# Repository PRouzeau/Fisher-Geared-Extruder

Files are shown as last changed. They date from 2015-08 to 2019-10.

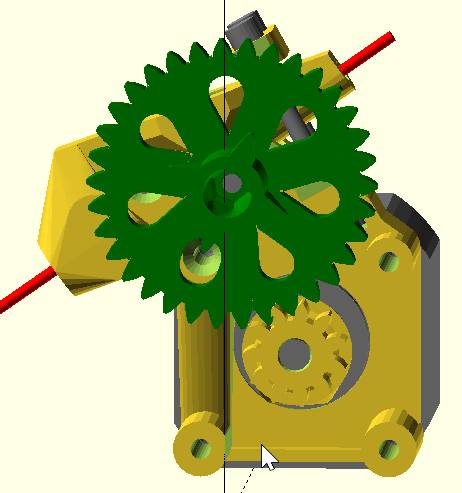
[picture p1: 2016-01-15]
Extruder_normal_pos.jpg

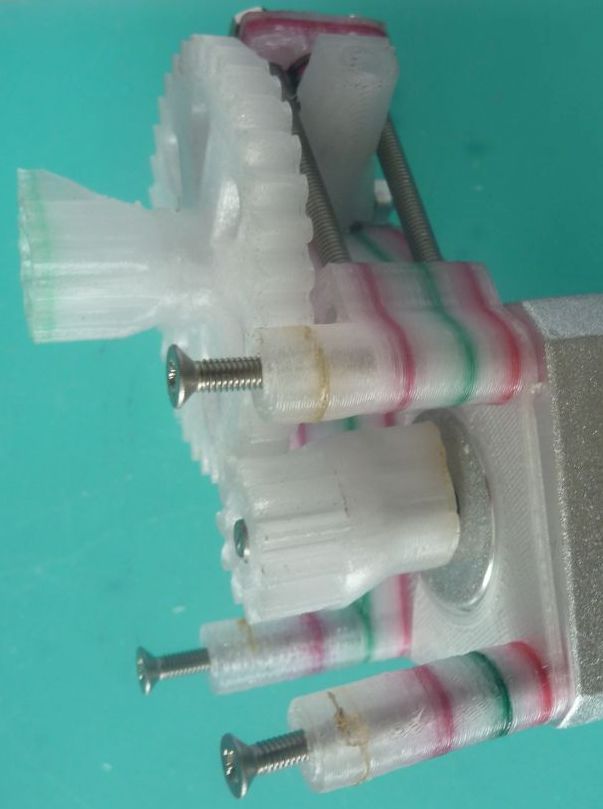
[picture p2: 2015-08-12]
Pres03.jpg

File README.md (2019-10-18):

# Geared-Extruder
Compact geared Extruder for bowden tube, side panel mount or top mount
designed initially for the Fisher Delta, used a mirrored version for the HXM.
Option with bearings 623 or MR93 (as supplied in Fisher 1)

To install OpenSCAD applications and models, see http://rouzeau.net/Print3D/OpenSCADApplications

Pour installer les applications et modèles OpenSCAD, voir  http://rouzeau.net/OpenSCAD/Applications

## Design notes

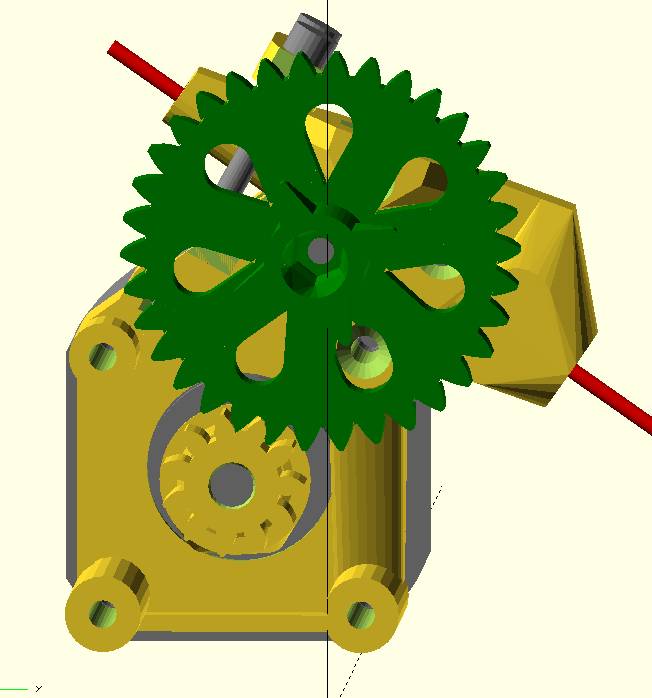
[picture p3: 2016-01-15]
Extruder_mirrored.jpg

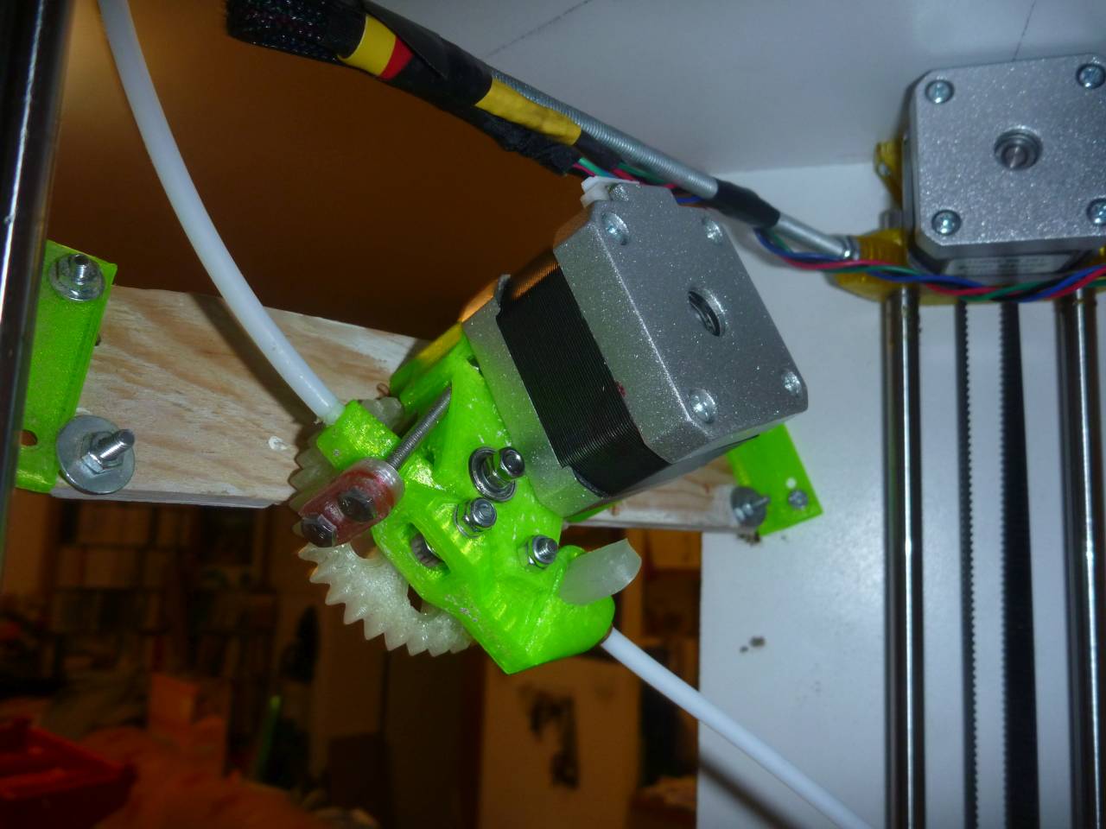
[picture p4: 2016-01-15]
HXM_extruder.JPG

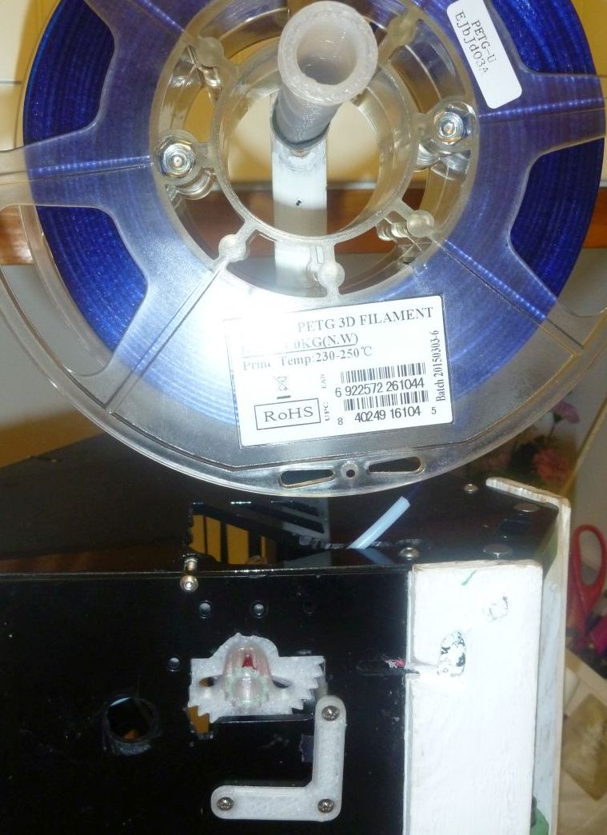
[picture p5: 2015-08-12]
Pres00.jpg

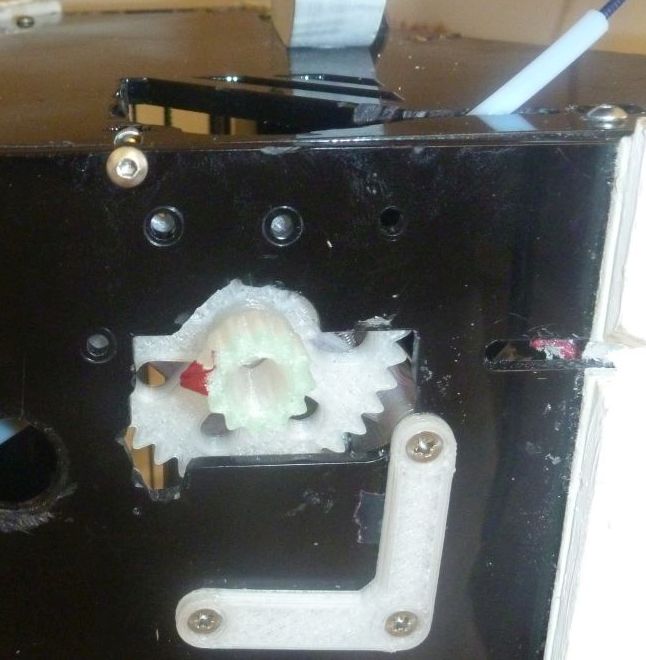
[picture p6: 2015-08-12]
Pres01.jpg

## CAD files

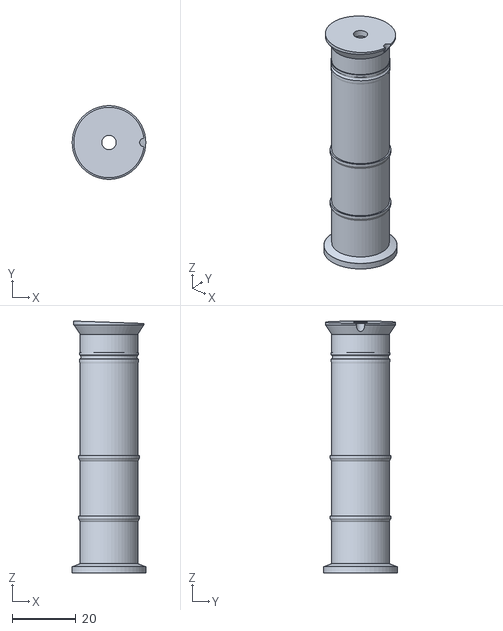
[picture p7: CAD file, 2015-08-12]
spigot80.stl
23.2 x 23.2 x 79.3

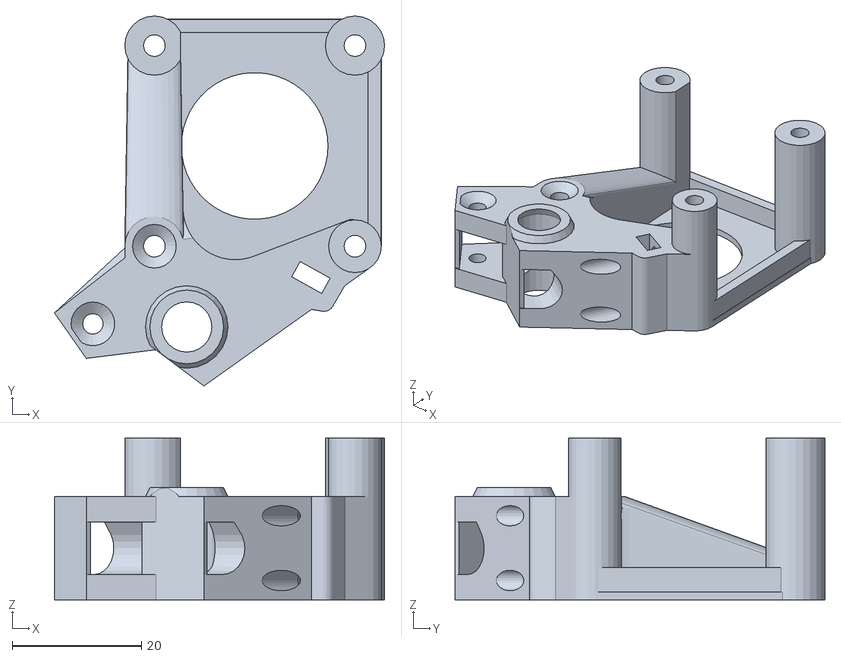
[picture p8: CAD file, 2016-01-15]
STL/Base_BB_MR93_mirrored.stl
51.0 x 57.2 x 25.0

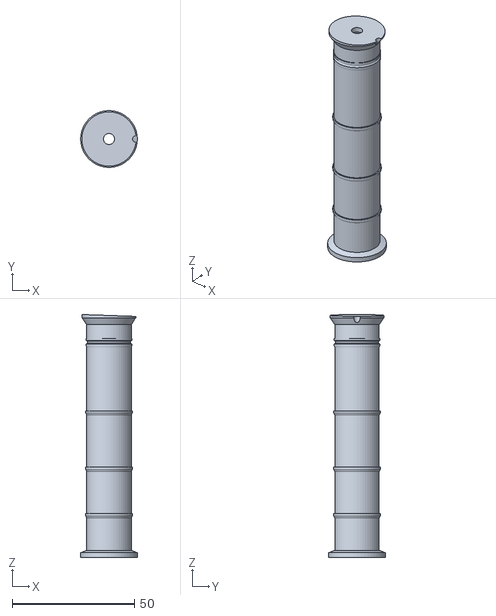
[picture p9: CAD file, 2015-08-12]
spigot100.stl
23.2 x 23.2 x 99.3

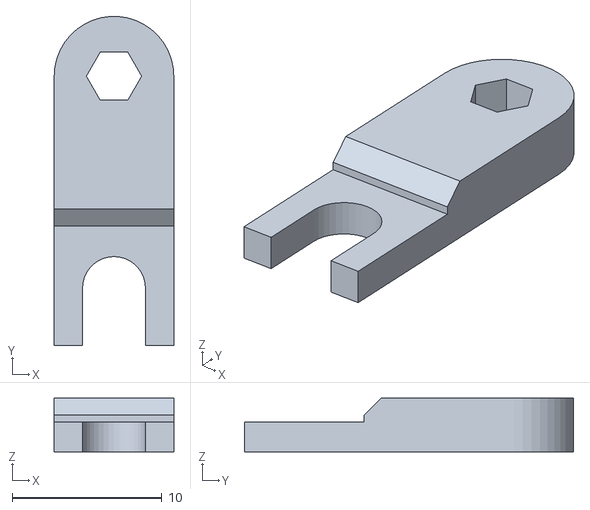
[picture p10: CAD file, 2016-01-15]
STL/tongue.stl
8.00 x 22.0 x 3.60

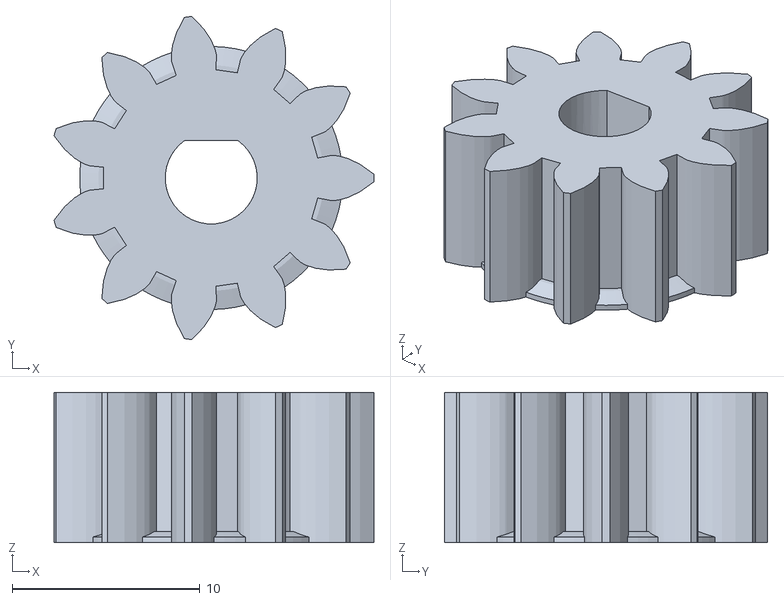
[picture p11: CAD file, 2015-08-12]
ormerod_small-gear.stl
17.0 x 17.2 x 8.00

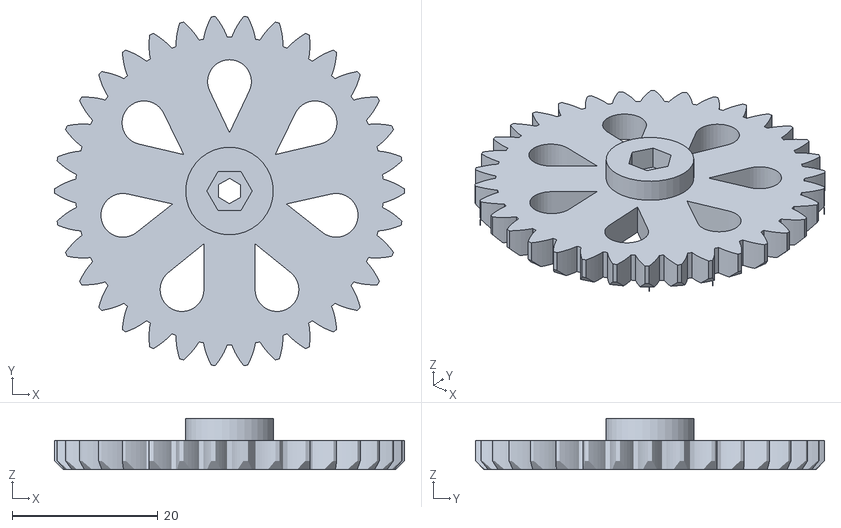
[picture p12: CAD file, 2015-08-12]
ormerod_large-gear.stl
48.0 x 47.8 x 7.00

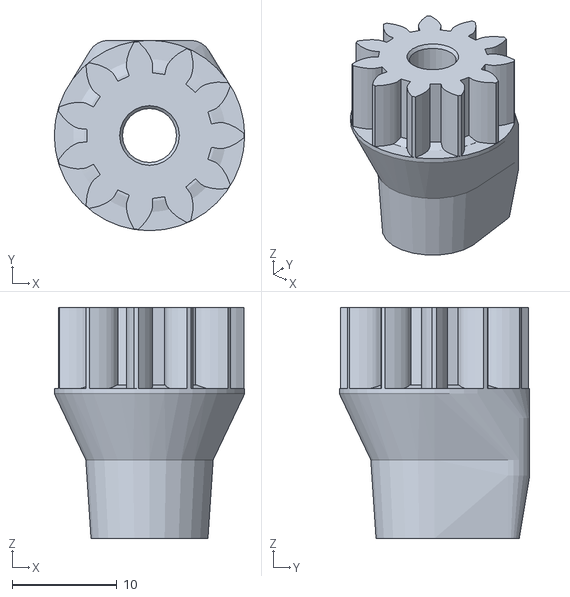
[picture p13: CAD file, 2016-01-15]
STL/PinionSize1.stl
18.1 x 18.1 x 22.0

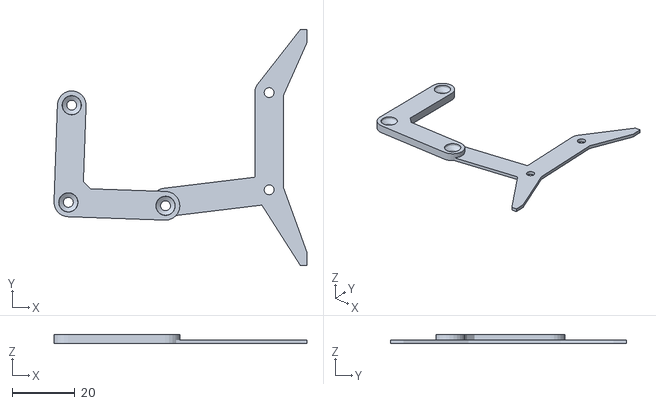
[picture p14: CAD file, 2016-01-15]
STL/motor_link_Fisher.stl
80.6 x 75.2 x 3.00

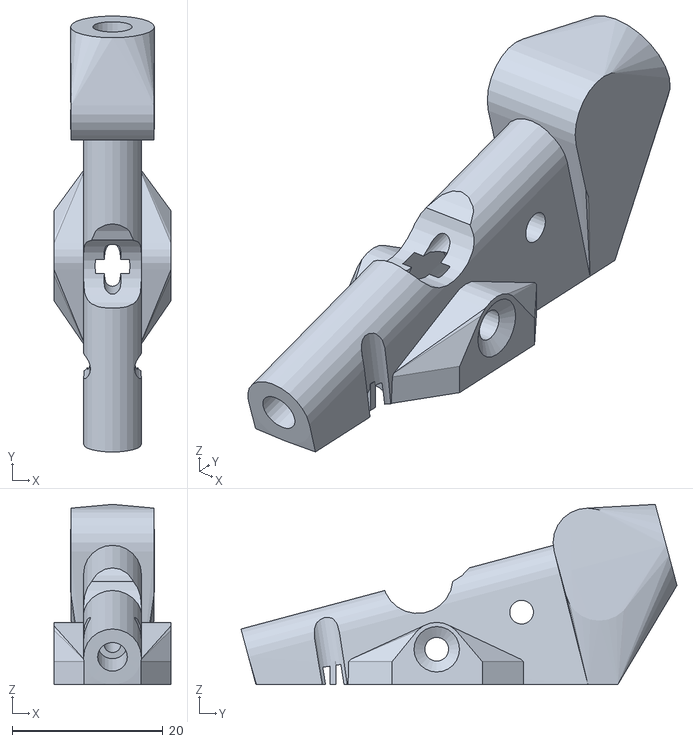
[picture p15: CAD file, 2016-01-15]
STL/lever.stl
15.5 x 57.9 x 23.9

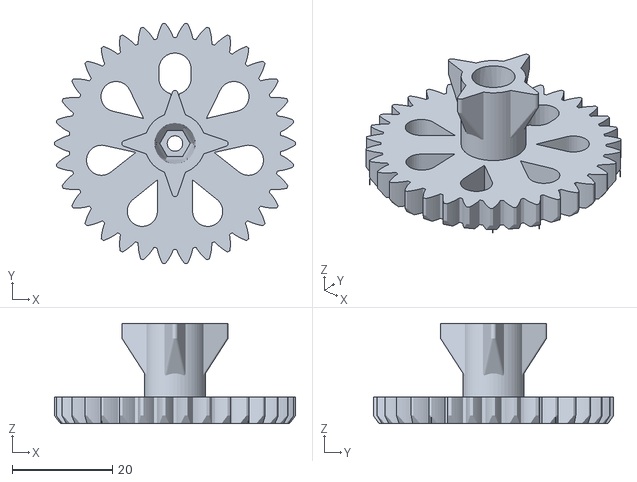
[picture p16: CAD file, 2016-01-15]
STL/lgear.stl
48.0 x 47.8 x 20.0

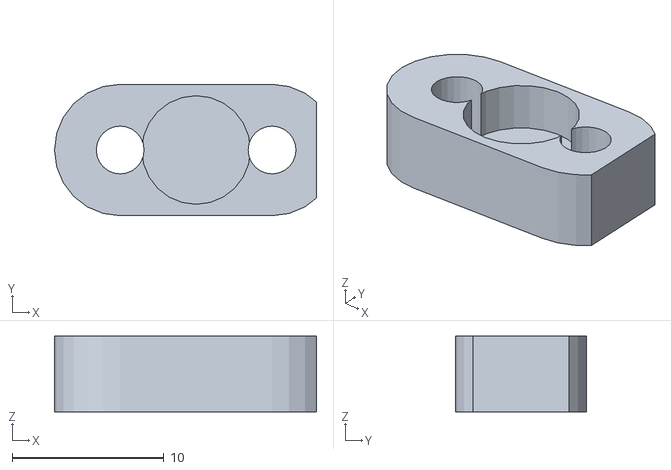
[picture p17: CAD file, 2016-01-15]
STL/pushpad.stl
17.2 x 8.65 x 5.00

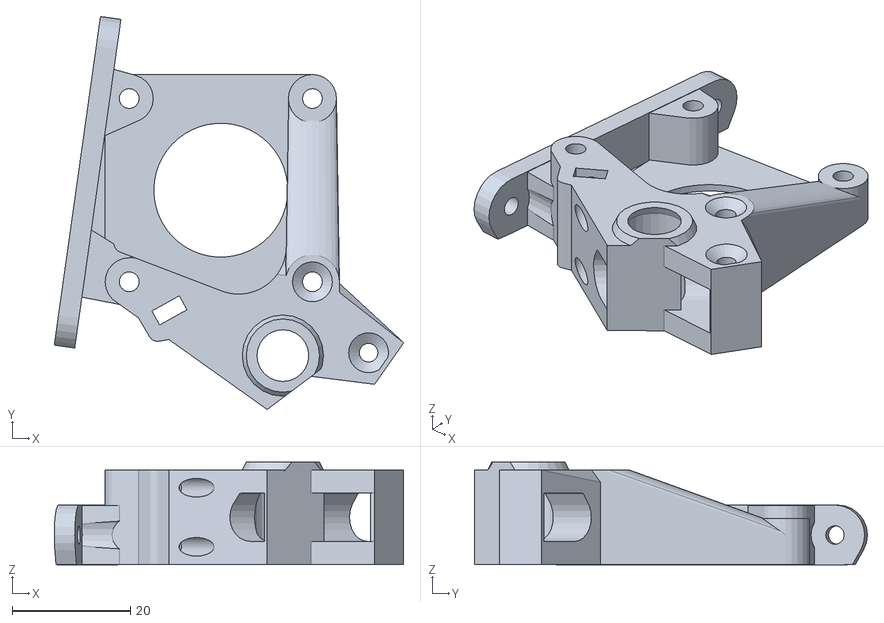
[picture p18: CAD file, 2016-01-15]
STL/Base_BB_623_Top_mount.stl
59.1 x 66.5 x 17.4

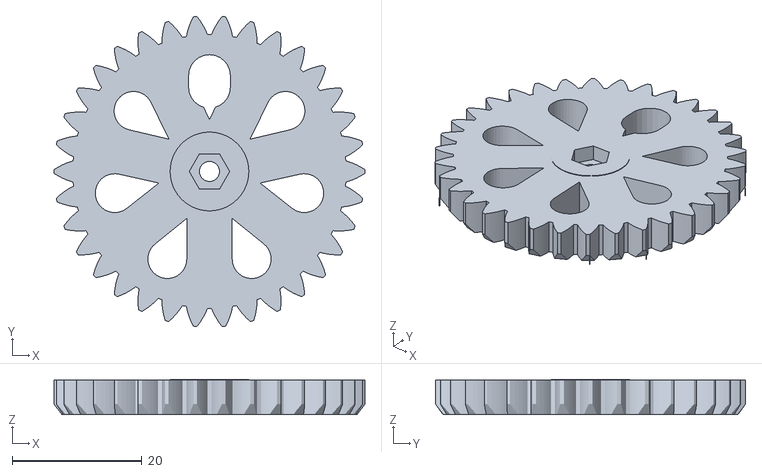
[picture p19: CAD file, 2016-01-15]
STL/lgear_no_thumbwheel.stl
48.0 x 47.8 x 5.40

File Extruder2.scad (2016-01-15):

/*Equipment design and all documents:  Copyright 2015-2016 Pierre ROUZEAU .
V. 15 Jan 2016
Equipment  license : OHL V1.2     Documents licence : CC BY-SA

GEARED EXTRUDER - was initially designed for the  RepRapPro printer Fisher Beta, then extended for other use and is now the extruder of 'HXM' printer.
It is a bit more complex than Fisher 1 extruder, but have following advantages :
- Better filament path while spool is on printer top
- Larger gear ratio (3.1 instead of 2), so more power
- Filament pressure adjustment accessible from top
- Could be opened from top for insert cleaning
- Shorter Bowden tube due to better path
Use the Fisher 1 kit with specific M3 hobbed insert of RepRapPro (used on all their printers).
Spring is the one of the Fisher extruder: external diameter 6.5mm, wire 0.8mm, length 7.5 mm
This extruder was designed to fit in the tight space of the fisher (in the fisher the extruder is inside the printer, between the arms), but could be used for any printer with 'Bowden' hotend. There is an alternative with top mount. It is also installed inside the HXM printer.
A template to position the extruder on Fisher is supplied. Be careful, the play between arms and motor with all carriages at top is less than 2mm (but your carriage are not supposed to go banging the supports, no ?)
The connection of the bowden is done with the specific RepRapPro 5mm brass insert. If needed, you could thread for another connection.

This is mechanics, so your machine shall be well calibrated and shall produce accurate dimensions. Gears (especially the pinion, shall be printed relatively slowly (50mm/sec) to produce more accurate teeth profile). Layer 0.2 for the gears. layers 0.2 or 0.25 for base and lever. You shall check that your printer have the same dimensions in X and Y if you want your gears being circular without hard point. The Fisher tend to create quite significant X/Y differences if the bed is tilted, which are not corrected by the calibration software.
    Note that DC42 fork of RRP firmware implement M579 command for scale correction since version 1.09m. see http://forums.reprap.org/read.php?146,593668
Printed in PETG on the Fisher, I really don't recommend to print it in PLA, that may be delicate to assemble without braking anything and there will be problem with the stepper temperature. ABS may be usable (but cannot be printed on a standard Fisher).
Recommended PETG yet: Reprapper. eSun PETG is NOT recommended (require very high temp and have many winding problems).
Supports are now incorporated to design and easier to remove, so do not activate support in your slicer for the base part.
It is an entirely original design, however the gears of the Ormerod extruder were reused (and slightly widened) and I get the idea to have the filament in the pressure lever from Ryan Carlyle extruder B'struder.
Driven by default  RepRapPro stepper 2.2 kg.cm
Assembly described here :
rouzeau.net/Print3D/FisherExtruder
BOM 
- 1 M3x25 Hex head screw for the hobbed drive - in fisher 1 kit
- 3 M3x35 countersunk screws for the stepper assembly on panel (thk 3mm)
- 2 M3x20 countersunk screws for lever articulation and push bearing
- 2 M3x40 screws (hex or cap head) for tensioner
- 1 M3x10 set screw for the pinion
- ordinary M3 nuts (lock is done with glue/resin)
- 1 medium size washer (large gear)
- 6 small sizes washer (4 for large gear and 2 for bearing)
- 3 bearings 623 (10x3x5) - option for 1*623 and 2*MR93 (Fisher 1)
- nut locking glue
- 1 M3 RepRapPro hobbed insert (dia 8) (only sold by them - in Fisher 1 kit)
- 1 spring diam ext 6.5mm, wire 0.8mm, len 7.5 mm (salvaged from Fisher extruder)
Printed parts (see program below):
Define first if the installation is mirrored or not (variable ismirrored)

- Base : N°2 with 623 bearings, 3 with MR93 bearings, 4 with top mount, 5 with top mount and 623 bearings
- Lever : N°6
- Large gear (34 teeth) : N°7
- Pinion (11 teeth): N°8,9,10 (three different sizes, smaller to larger)
- Lever pushing pad : N°11
- template/screw holder for panel fixation : N°12
- tongue for Bowden brass end (original could be reused)

Note there is 2 sizes for the pinions (0 and 1), to adapt with minimum play. There won't be too much wear if there is play in gears, but that makes clik-clak noises during retract. 
If the play is unsufficient with the smaller pinion, you may check your extrusion rate (do not overextrude) and the accuracy of your prints. 
  There shall be no hard point while rotating manually the thumbwheel. 
  If you print pinion alone, you can print two in the same time as one, because the printing time is dictated by the cooling time between layers (25 sec. for PETG if no parametrable cooling). 
  
There is now the parameter 'ismirrored' to mirror the extruder. Note that for 'HXM' printer, you shall use the mirrored version.   

Another new option is main gear without thumbwheel, if more practical to use the gear itself for feeding. 
  
*/

include <PRZutility.scad>
//-- Parameters modifiable by user ------------------------
insertdia = 5.1; // bowden brass insert diam 5
inletTube = 3.8;  //inlet tube diameter  if =0 -> inlet is a cone
htot = 25;      // columns height - this is the minimum for shaft clearance

qpart=1;
ismirrored = false;

if (qpart) {
  if (qpart==1) mirrory(ismirrored) tsl (-25,-4,36+8) rot (-90) extruder(false); // whole extruder
  if (qpart==92) mirrory(ismirrored) tsl (-25,-4,36+8) rot (8)extruder(true); // whole extruder with top mount 
  if (qpart==93) mirrory(ismirrored) tsl (-25,-4,36+8) rot (8)extruder(false,true); // option Fisher 1 (bearing MR93)
    
  else if (qpart==2) mirrorx(ismirrored) rot (0,-90) base(false); // extruder chassis
  else if (qpart==3) mirrorx(ismirrored) rot (0,-90) base(false,true); // extruder chassis - MR93 bearings
  else if (qpart==4) mirrorx(ismirrored) rot (0,-90) base(true); // extruder chassis - top mount
  else if (qpart==5) mirrorx(ismirrored)  rot (0,-90) base(true,true); // extruder chassis - MR93 bearings  - top mount

  else if (qpart==6) mirrorx(ismirrored) rot (90) rot(-lvang-angflat) lever(); 
  
  else if (qpart==7) rot (0,-90)  lgear2();  // gear wheel  
  else if (qpart==8) rot (0,-90)  sgear2(); // pinion  size '0' (normal play)
  else if (qpart==9) rot (0,-90)  sgear2(1);// pinion  size '1' (less play)
    
  else if (qpart==10) rot (0,-90)  lgear2(0); // gear wheel without thumb wheel
   
  else if (qpart==11) rot (-tsang+90)  pushpad(); // spring pusher
  else if (qpart==12) motorlink();
}

//cylz (45,10, 0,0,2);
//cylz (14.5,5, 0,0,15);

//-- do not touch if you don't know ----------------------------------

springhole = 7; // spring 6.5 mm
boltspace = 10;
boltheaddia = 0; // 5.4 for inserted head (~tiny walls);
thk=16;

hobby = -12.48; // big wheel articulation
hobbz = 5;

levery = -12; // lever articulation
leverz = -9.5;

pushy = hobby-8; // push bearing
pushz = hobbz-5.6;

lvposy = 5.5; // lever position
lvposz = -15; 

nutalign =23.5;

lvang=35;
angflat = -15;
tsang = lvang-6;

holeplay = 0.15; // diameter increase for all cylinders (internals/external) and off-axis dimension increase for cuben primitives. Not sufficient for small vertical holes.
   //Beware that this increase is the same whatever the axis, so for vertical cylinder holes, you may add other clearance

// misc. parameters
diamNut3 = 6.1; // checked
diamNut4 = 8.1; // checked

//distaxe = sqrt ((hobby-31/2)*(hobby-31/2)+(hobbz-31/2)*(hobbz-31/2)) ;
// echo (distaxe=distaxe); // check axis/axis distance conformity with Ormerod gears

*pan();

module motorlink() {
   //motor bolts link
  h=3;
  difference () {
    union() {
      rotz(-2) {
        hull() duplx (31) cylz (9,h);
        hull() duply (31) cylz (9,h);
      }  
      rotz(45) cubez (8,8,h, 4);
      hull() { 
        cylz (9,1.2, 31);
        cylz (9,1.2, 31+33,4);
      }  
      hull() 
        duply (31) cylz (9,1.2, 31+33,4);
      hull() {
        cylz (9,1.2, 31+33,4);
        cubez (2,4,1.2, 31+33+11, -18);
      }
      hull() {
        cylz (9,1.2, 31+33,4+31);
        cubez (2,4,1.2, 31+33+11, 31+22);
      }
      // cubez (12,30,1,  31+33+6); check
   }  
   tsl (0,0,1)
     rotz(-2) 
     duplx (31) duply(31) { 
       cylz (-3,66);
       cylinder(d2=6.1, d1=3, h=1.2); 
       cylz (6, 5, 0,0,1.19);}
   duply (31) cylz (-3,66, 31+33,4);     
  }
}

module pan() {   // not used - was for panel placement
  tsl (0,-20, 26) // side panel
    rot (90,-90,90)
      linear_extrude(height = 3, center = false)
        import("panelex.dxf");
  color ("red") cubez (200,200,6);    
  color ("red") cubez (60,10,76,  -30, -47);
  tsl (-60,-44, 85)
  rot (-26)
  color ("red") cubex (60,10,172);
}
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

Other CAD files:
STL/Base_BB_623.stl
STL/base_BB_MR93.stl
STL/lever_mirrored.stl
STL/Base_BB_MR93_Top_mount_mirrored.stl
STL/Base_BB_623_Mirrored.stl
PRZutility.scad
STL/Base_BB_623_Top_mount_mirrored.stl
STL/Base_BB_MR93_Top_mount.stl
STL/PinionSize0.stl

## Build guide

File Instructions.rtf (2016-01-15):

Equipment design and all documents: Copyright Pierre ROUZEAU 2015-2016.
V. 15 Jan 2016 – reinforcment of bearing support – mirrored version.
Equipment license : OHL V1.2 Documents licence : CC BY-SA
GEARED EXTRUDER
Initially designed for printer Fisher Beta, then extended for other uses.
Use the specific M3 hobbed insert of RepRapPro (sold by Think3DPrint3D or robofun.ch) but not the original hobbed insert of the Fisher Beta. Simplest is to buy the Fisher 1 kit for geared extruder.
Spring is the one of the Fisher extruder: external diameter 6.5mm, wire 0.8mm, length 7.5 mm
This extruder is specifically designed to fit inside a printer (in the fisher the extruder is inside the printer, between the arms), but could be used for any printer with 'Bowden' hotend
A template to position the extruder on Fisher is supplied. Be careful, the play between arms and motor with all carriages at top is less than 2mm (but your carriage are not supposed to go banging the supports, no ?)
The connection of the bowden is done with the specific RepRapPro 5mm brass insert. If needed, you could thread for another connection or modify file to set a M4 nut.
This is mechanics, so your machine shall be well calibrated ans shall produce accurate dimensions. Gears (especially the pinion, shall be printed relatively slowly (50mm/sec) to produce more accurate teeth profile). Layer 0.2 for the gears. layers 0.2 or 0.25 for base and lever. Note that DC42 fork of RRP firmware implement M579 command for scale correction since version 1.09m. see http://forums.reprap.org/read.php?146,593668
Printed in PETG on the Fisher, I really don't recommend to print it in PLA, that may be delicate to assemble without broke anything and there will be problem with the stepper temperature. ABS may be usable (but cannot be printed on a standard Fisher).
Recommended PETG yet: Reprapper. eSun PETG is NOT recommended (unworkable without this geared extruder due to poor winding, so egg and chicken problem here).
Now the supports are incorporated in the design and you shall not activate support in your slicer. So it is now possible to group parts for printing.
It is an entirely original design, however the gears of the Ormerod extruder were reused (and slightly enlarged) and I get the idea to have the filament in the pressure lever from Ryan Carlyle extruder.

Note there is 2 sizes for the pinions (0 and 1), to adapt with minimum play. There won't be too much wear if there is play in gears, but that makes clik-clak noises during retract.
If the play is unsufficient with the smaller pinion, you may check your extrusion rate (do not overextrude) and the accuracy of your prints.
There shall be no hard point while rotating manually the thumbwheel.
If you print pinion alone, you can print two in the same time as one, because the printing time is dictated by the cooling time between layers (25 sec. for PETG if no parametrable cooling).
There is now the parameter 'ismirrored' to mirror the extruder. Note that for 'HXM' printer, you shall use the mirrored version (see image).
Another new option is main gear without thumbwheel, if more practical to use the gear itself for feeding.
To lock inlet tube, thread the tube with a M4 nut and tap the lever hole with an M4 screw.
Driven by default RepRapPro stepper 2.2 kg.cm
Assembly described here :
rouzeau.net/Print3D/FisherExtruder
BOM
- 1 M3x25 Hex head screw for the hobbed drive
- 3 M3x35 countersunk screws for the stepper assembly on panel (thk 3mm)
- 2 M3x20 countersunk screws for lever articulation and push bearing
- 2 M3x40 screws (hex or cap head) for tensioner
- 1 M3x10 set screw for the pinion
- ordinary M3 nuts (lock is done with glue/resin)
- 1 medium size washer (large gear)
- 6 small sizes washer (4 for large gear and 2 for bearing)
- 3 bearings 623 (10x3x5) - option for 1*623 and 2*MR93 (Fisher 1 kit)
- Nut locking glue
- 1 M3 RepRapPro hobbed insert (dia 8) (sold by THINK3DPRINT3D)
- 1 spring diam ext 6.5mm, wire 0.8mm, length 7.5 mm (salvaged from Fisher extruder)
Printed parts (see program below):
Note that to get the parts mirrored, you shall set 'ismirrored=true ;'
- Base : N°2 (BB 623), N°3 (BBMR93) ,N°4 (BB623, top mount) or N°5 (BBMR93, top mount)
- Lever : N°6
- Large gear with thumbwheel (34 teeth) : N°7
- Large gear without thumbwheel (34 teeth) : N°10
- pinion (11 teeth): N°8, 9 (2 sizes, smaller to larger)
- Lever pushing pad : N°11
- template/screw holder for panel fixation : N°12
- tongue for Bowden brass end (original could be reused)

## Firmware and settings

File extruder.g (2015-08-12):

;modified data for geared extruder - add at the end of your config file, or modify lines 

M569 P4 S0				; Drive 4:  extruder goes backwards. Reverse from original due to geared transmission
M566 E600				; Maximum instant speed changes mm/minute  extruder max speed change from 1200 to 600
M906 E1000				; Set motor currents (mA) Extruder I from 1200 to 1000 - geared - do not set too low for good retract
M201 E2000				; Accelerations (mm/s^2)  Extruder acceleration from 4000 to 2000 - geared
M92 E420.0				; extrusion rate, with geared extruder - copied from Ormerod, nearly exact

; and in your slicer profile, retract speed reduced to 80mm/s

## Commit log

2015-08-12 First commit
    Compact geared extruder designed for RepRapPro Fisher Delta. Can be used
    for any bowden hotend with minor modifications. Side mount on panel.
    [Extruder2.scad, PRZutility.scad, extruder.g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]
2015-09-08 Added 2 larger size for pinion
    There was too much play, making noise during retract, so I added 2
    pinions of larger size.
    [Extruder2.scad, PRZutility.scad]
2015-12-20 Add MR93 bearing option and top mount option
    [Extruder2.scad]
2016-01-15 Reinforcment of bearing containment, mirroring position
    The bearing is now better maintained, so less play with gears. Option
    for mirrored position, add STL files. Option for flat large gear.
    [Base_BB_623.stl, Base_BB_623_Mirrored.stl, Base_BB_623_Top_mount.stl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]
